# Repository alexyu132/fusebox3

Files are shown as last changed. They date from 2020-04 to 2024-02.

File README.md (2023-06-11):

:warning: **Still under active development**: Parts and documentation may change!
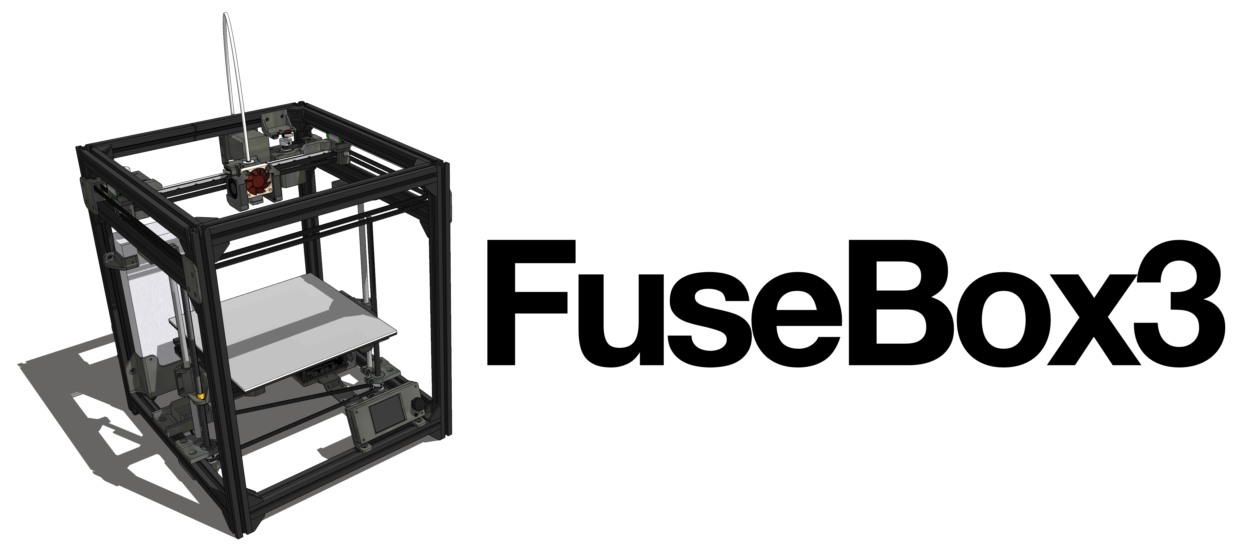
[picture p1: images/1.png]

## The latest in the FuseBox line of 3D printers.

FuseBox3 is a midsize CoreXY printer designed for fast printing and high output quality.

Specs:
- Safe build area (XYZ): 235x235x235mm (Absolute max travels: 238x238.75x238mm)
- Frame dimensions (XYZ): 350x372x427mm
- CoreXY movement system running on MGN9/MGN12 rail
- 2020 extrusion frame
- E3D v6 type hotend with Bowden extruder
- Dual leadscrew, belt-driven z-axis
- Dual 4010 blower print cooling + 4010 axial fan hotend cooling

## Quick Links
### [BOM](documentation/BOM.md)

# Design and changes from FuseBox2/R
While the original FuseBox and FuseBox2 were optimized for simplicity and low build cost, FuseBox3 targets a more premium price point without being overly expensive. However, accessibility and ease of construction is still a priority. Therefore, the printer needs no custom CNC'd parts, and all parts were picked to be easily sourceable online.

### Linear rails
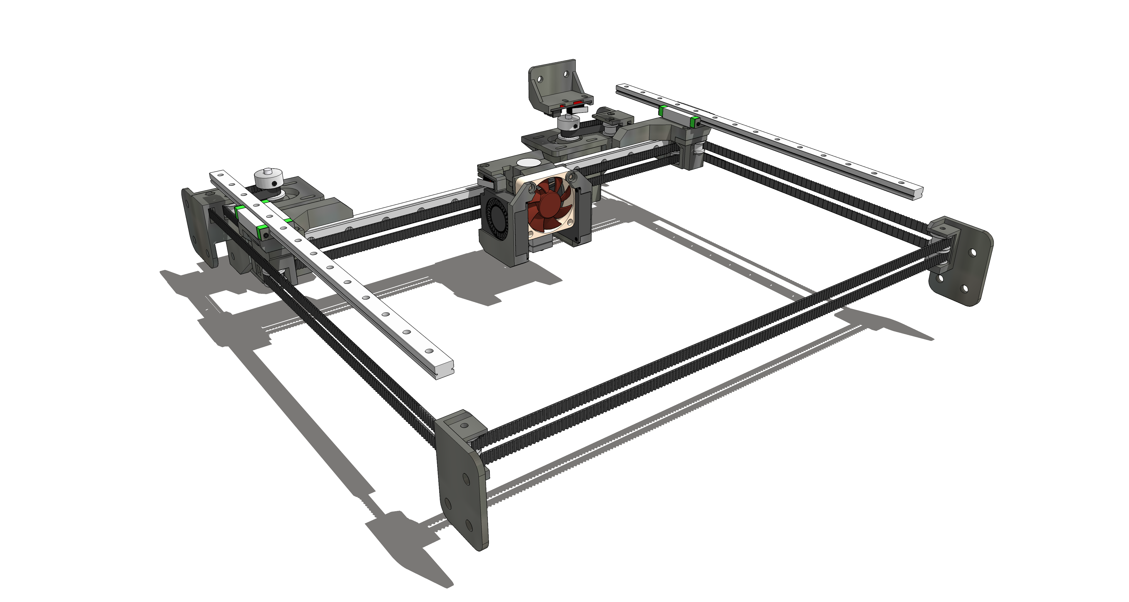
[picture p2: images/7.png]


With MGN-style linear rails becoming cheaper and more easily available, the CoreXY movement has been redesigned to ride completely on rails - the y-axis now uses MGN9 rails screwed directly to the extrusions, which improves rigidity compared to the old linear rods. Like on the Fusebox2R, the gantry/x-axis uses a single MGN12 rail, although it's now 50mm longer to account for the additional build area.

### Belt path changes, tensioning improvements
The original FuseBox and FuseBox2 share a similar belt path - the motors are mounted in the corners of the frame, and the motor pulleys serve as the "ends" of the belt path on the back side. This belt path design minimizes the number of idler pulleys needed, at the cost of quite a bit of wasted space in the x direction, necessitating a wider frame.

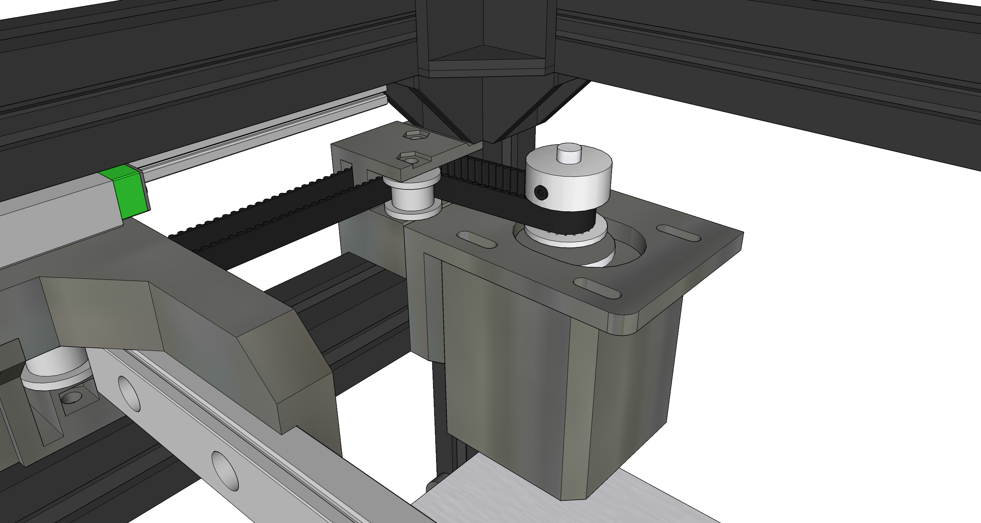
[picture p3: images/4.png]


On the FuseBox3, two additional idlers have been added on the rear (motor) side to bring the belts as close to the sides of the frame as possible. This allows the FuseBox3's frame to be 42mm shorter in the x direction than the FuseBox2R's, while simultaneously having an additional 25mm of x-axis travel. The motors have been relocated to the very back of the machine, just underneath the top rear horizontal extrusion. The motor mounts now have slotted screw holes, allowing them to slide to adjust belt tension. On the FuseBox and FuseBox2, tensioning was done by manually pulling on the belts and sliding them into carriage-mounted belt clamps. The new tensioning system should significantly simplify the belt mounting and tensioning process.

Additionally, the front idler brackets have been changed so that the top and bottom idlers are stacked on top of each other rather than offset. This makes the idlers easier to assemble and saves a bolt and nut on each side.

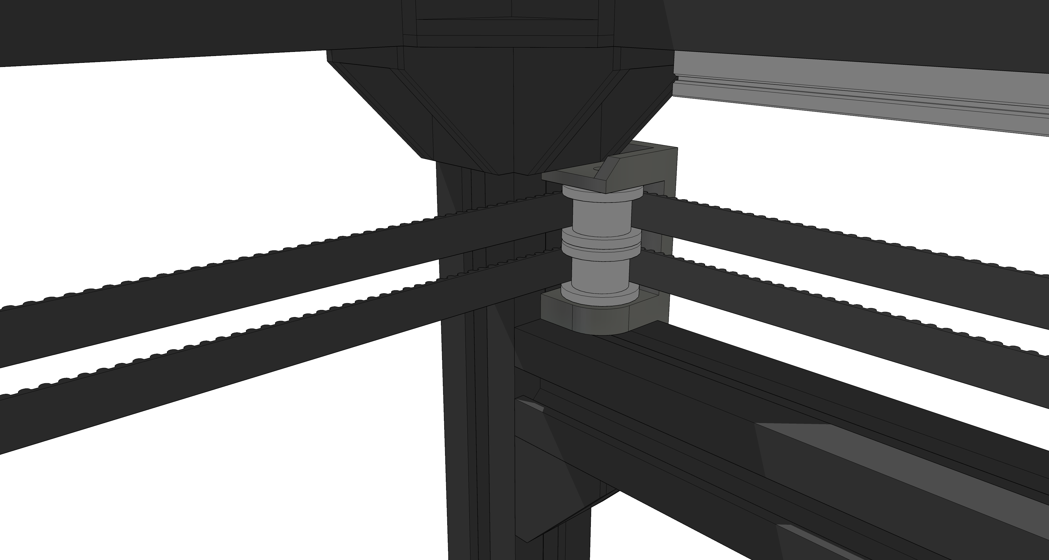
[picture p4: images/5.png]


### Z-axis

The z-axis keeps the 8mm rods due to space and cost constraints, but is now reconfigured as a fully belt-driven setup. On the prototype FuseBox2, the cantilevered z-axis was slightly susceptible to vibration and was also susceptible to banding if lower quality leadscrews or bearings were used. The new design's rods have been relocated to the sides of the printer, with each end driven by its own belt loop. These are connected to a single Z motor, which drives them via a 4:1 reduction pulley. The belted design eliminates banding artifacts and greatly increases the max Z speeds achievable.

### Hotend carriage, print cooling
The general arrangement of FuseBox3's carriage is very similar to the carriage on the older FuseBox2R, with the main differences being the print cooling setup and the belt mounting method. Subjectively, it's also a lot tidier in appearance than the earlier carriage designs.

Like the carriage on the FuseBox2R, the new carriage keeps the mass vertically centered on the rail, with the belts also centered and kept as close to the rail as possible. This design minimizes any twisting of the print head during sharp directional changes.

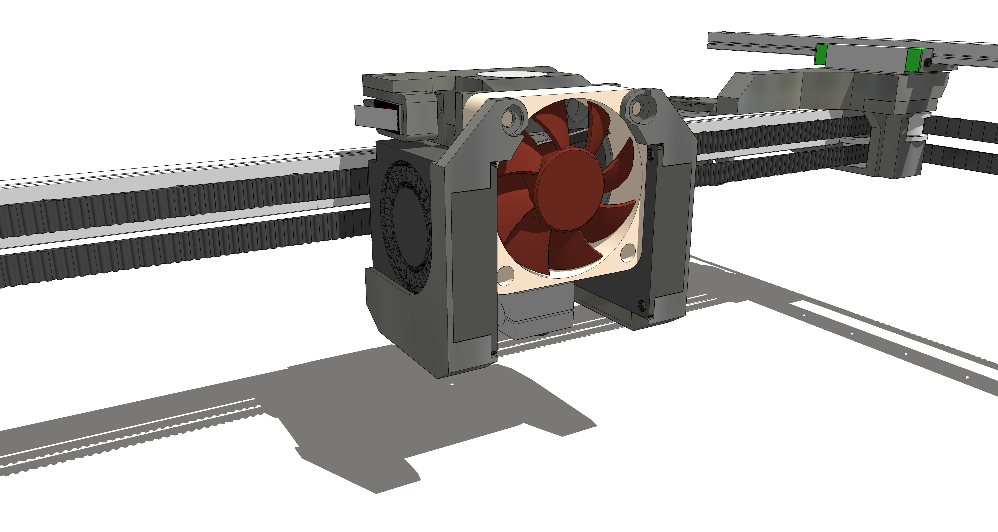
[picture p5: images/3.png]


Since the FuseBox3 has sliding motor mounts, tensioning is no longer done on the carriage. The belts are now attached to the carriage by a pair of clamp pieces that screw into the main carriage body. The clamps have a small cutout on the inner side for routing excess belt, so the belts don't have to be shaved to a precise length like they do on the FuseBox2R.

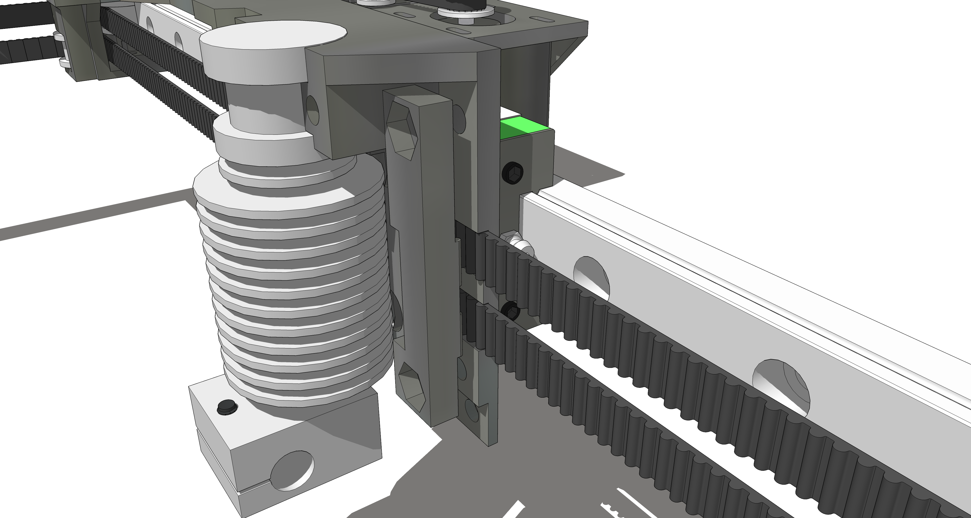
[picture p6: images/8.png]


The print cooling setup swaps out the single 4020 blower for twin 4010 blowers flanking the hotend. The old single blower design provided relatively good cooling performance, but the one-sided airflow led to weaker cooling with certain overhang orientations. Twin blowers enable more even part cooling coverage, and the much shorter ducts provide less airflow restriction. The 40mm axial fan for the hotend has been retained, as it provides lower noise than a 30mm fan for equivalent airflow.

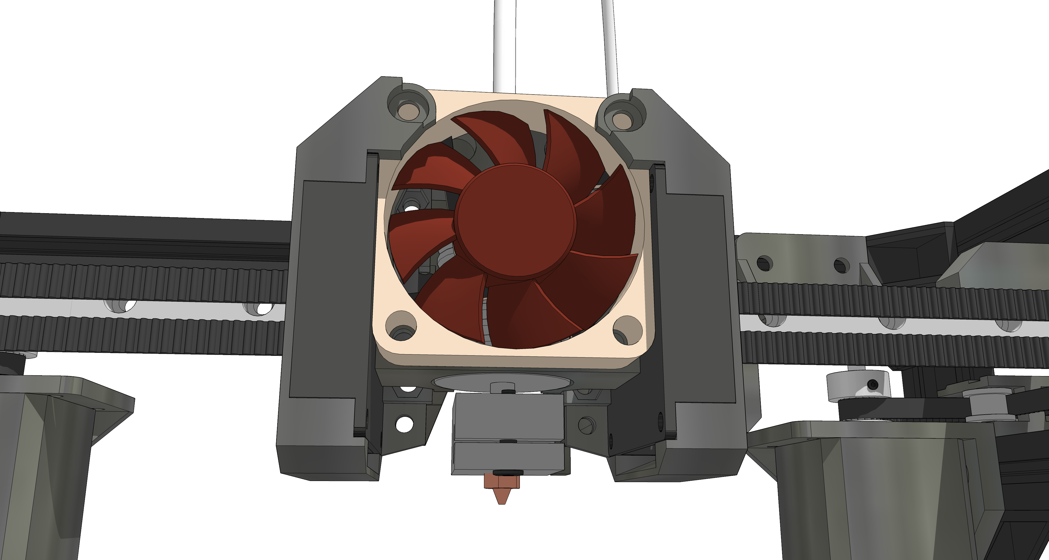
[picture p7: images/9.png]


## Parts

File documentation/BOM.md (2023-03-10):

# Recommended Suppliers (US)
- Extrusions: Misumi (US-based)
- Pulleys, closed loop belts: Powge (Aliexpress)
- Open loop belts: Trianglelab (Aliexpress), Powge (Aliexpress)

# BOM - Non-printed

## Frame
### Extrusions

| Item | Quantity  | Notes|
|---|---|-----|
| 2020 extrusion, 407mm (407mm minimum, these can be increased to 410mm or more to give more room at the bottom of the printer) | 4  | Z axis |
| 2020 extrusion, 332mm | 4  | Y axis. The Y extrusions can be lengthened to increase Y travel without needing to modify any other components. To be able to use 300mm MGN9 rails on the Y axis, the Y extrusions should be at least 345mm, and the top Y extrusions should be at least 385mm. |
| 2020 extrusion, 372mm | 2  | Top Y axis. Must be 40mm longer than Y axis extrusions. |
| 2020 extrusion, 310mm | 4  | X axis |
| 2020 extrusion, 260mm | 2  | Bed X axis |
| 2020 extrusion, 120mm | 2  | Bed Y axis |

### Brackets and fasteners
There are two options for joining frame extrusions. The easiest and quickest, but more expensive, option is to use corner brackets everywhere. The second option is to tap the ends of the extrusions and join them with M5 hardware. This will also require access holes to be drilled through some of the extrusions. Note that this option still requires a few corner brackets to prevent certain extrusions from twisting. The required brackets are marked in yellow in the Sketchup file.

**Option 1: All corner brackets**

| Item | Quantity  |
|---|---|
| Corner bracket (20x20x17mm) | 32 |
| M5x8mm button head | 64 |
| M5 T nut | 64 |

**Option 2: Tapped ends**

| Item | Quantity  |
|---|---|
| Corner bracket (20x20x17mm) | 8 |
| M5x8mm button head | 16 |
| M5 T nut | 16 |
| M5x12mm button head | 24 |
| M5 washer | 24 |

## CoreXY movement (excluding print head)

| Item | Quantity  |
|---|---|
| MGN9 linear rail with MGN9H block, 280mm long (can use 300mm length if Y extrusions are extended, see extrusions section above) | 2 |
| MGN12 linear rail with MGN12C block, 300mm | 1 |
| M3 T nut | 8 |
| M5 T nut | 20 |
| M3x6mm socket head | 8 |
| M3x8mm socket head | 16 |
| M5x8mm button head | 20 |
| M3x10mm button head | 12 |
| M3x20mm button head | 8 |
| M3x30mm button head | 2 |
| M3 nylon lock nut | 22 |
| M3 washer | 8 |
| 16T toothed 2GT idler, 3mm bore | 8 |
| 16T smooth 2GT idler, 3mm bore | 4 |
| 20T 2GT pulley, 5mm bore | 2 |
| 2GT 6mm width belt | 3M |
| NEMA 17 stepper (60+ oz-in/42+ N-cm preferred) | 2 |
| PCB endstop | 1 |

## Print head
| Item | Quantity  |
|---|---|
| M3x6mm socket head | 4 |
| M3x25mm button head | 2 |
| M3x16mm button head | 4 |
| M3x10mm button head | 7 |
| M3 nylon lock nut | 13 |
| E3D V6 or Lite6 hotend (Bowden) | 1 |
| 4010 blower fan (ball bearing recommended) | 2 |
| 4010 axial fan (ball bearing recommended)| 1 |
| Omron D2F-L microswitch (cut one off a PCB endstop) | 1 |

Note: The blower shrouds and axial fan can optionally be attached by zip ties instead of screws. This gets rid of four M3x16mm bolts, two M3x10mm bolts, and six M3 lock nuts.

## Z axis
| Item | Quantity  |
|---|---|
| M3x8mm socket head | 4 |
| M3x10mm button head | 14 |
| M3x20mm button head | 1 |
| M5x8mm button head | 32 |
| M5 T nut | 32 |
| M3 nylon lock nut | 15 | 
| 8mm leadscrew (300mm length, 2mm lead) and brass nut | 2 |
| 300mm length 8mm OD smooth rod | 2 |
| 710mm closed loop 2GT belt, 6mm width | 1 |
| 20T 2GT pulley, 8mm bore | 2 |
| 20T 2GT pulley, 5mm bore | 1 |
| LM8LUU bearing | 2 |
| 608 bearing | 4 |
| NEMA 17 pancake stepper (up to 25mm motor body length) | 1 |
| Ender 3 compatible heated bed (235mmx235mm) and leveling hardware (M4x55 or M4x60mm screws, 8mm OD 40mm length springs) | 1 |
| PCB endstop | 1 |

## Power supply
| Item | Quantity  |
|---|---|
| M5x8mm button head | 5 |
| M5 T nut | 5 |
| M4x6mm socket head | 3 |
| M3x10mm button head | 2 |
| M3 nylon lock nut | 2 |
| Meanwell LRS-350-24 power supply | 1 |
| IEC socket with fuse and switch | 1  |
| IEC power cord | 1  |

## Stock extruder (Bowden)
This is pretty much the extruder from the FuseBox2, modified to hang below an extrusion instead of to the side. Can print flexible filament.

| Item | Quantity  |
|---|---|
| M5x8mm button head | 2 |
| M5 T nut | 2 |
| M3x8mm socket head | 3 |
| M3x10mm button head | 1 |
| M3x25mm button head | 1 |
| M3 nylon lock nut | 1 |
| Stiff spring | 1 |
| 625 bearing | 1 |
| MK8 extruder gear | 1 |
| NEMA 17 stepper (60+ oz-in/42+ N-cm preferred) | 1 |
| PC4-M6 Bowden coupler | 1 |

## Controller and LCD

### BTT SKR and TFT24
| Item | Quantity  |
|---|---|
| M5x8mm button head | 5 |
| M5 T nut | 5 |
| M3x25mm button head | 4 |
| M3x10mm button head | 9 |
| M3 nylon lock nut | 5 |
| M3 nylon standoff, 30mm length | 4 |
| BTT SKR 1.3 or 1.4 | 1 |
| BTT TFT24 LCD | 1 |

## Miscellaneous

| Item | Quantity  |
|---|---|
| 235x235mm print surface (PEI recommended) | 1  |
| Zip ties | Varies  |
| Cable mesh (optional) | Varies  |
| 18AWG wire for AC input | Varies  |
| 14AWG wire for main DC power | Varies  |
| Small binder/bulldog clips for bed | 4  |
| Adhesive felt or rubber feet | 4  |

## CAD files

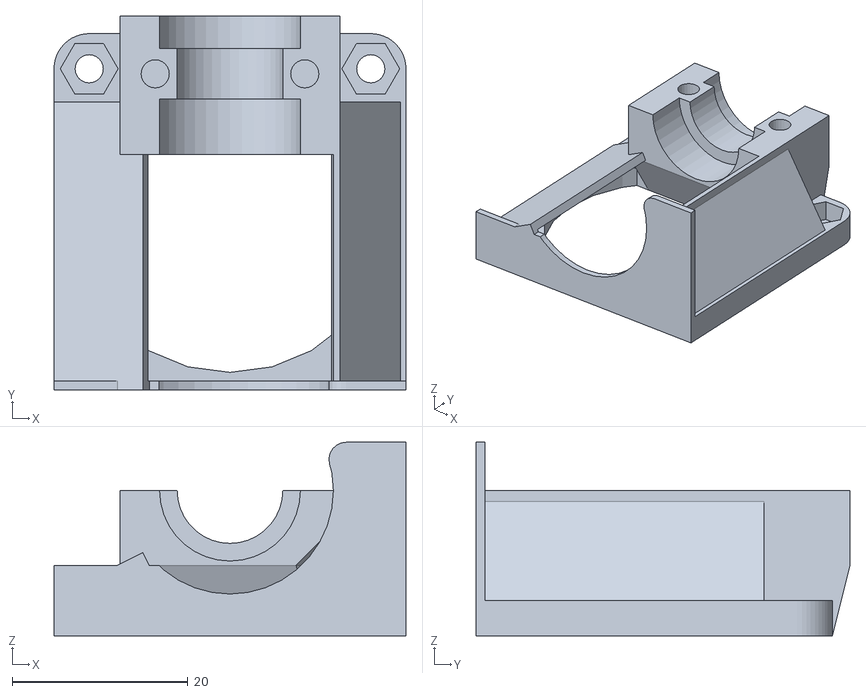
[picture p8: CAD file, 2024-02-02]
stl/carriage/hotend bracket.stl
40.0 x 42.5 x 22.0

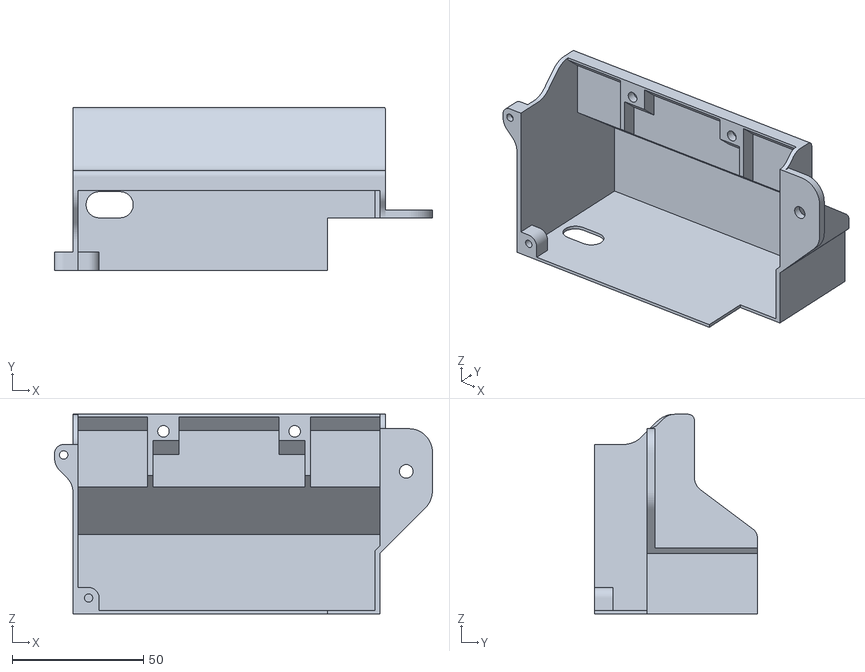
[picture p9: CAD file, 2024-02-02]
stl/electronics/meanwell psu bracket large.stl
144.0 x 62.0 x 76.0

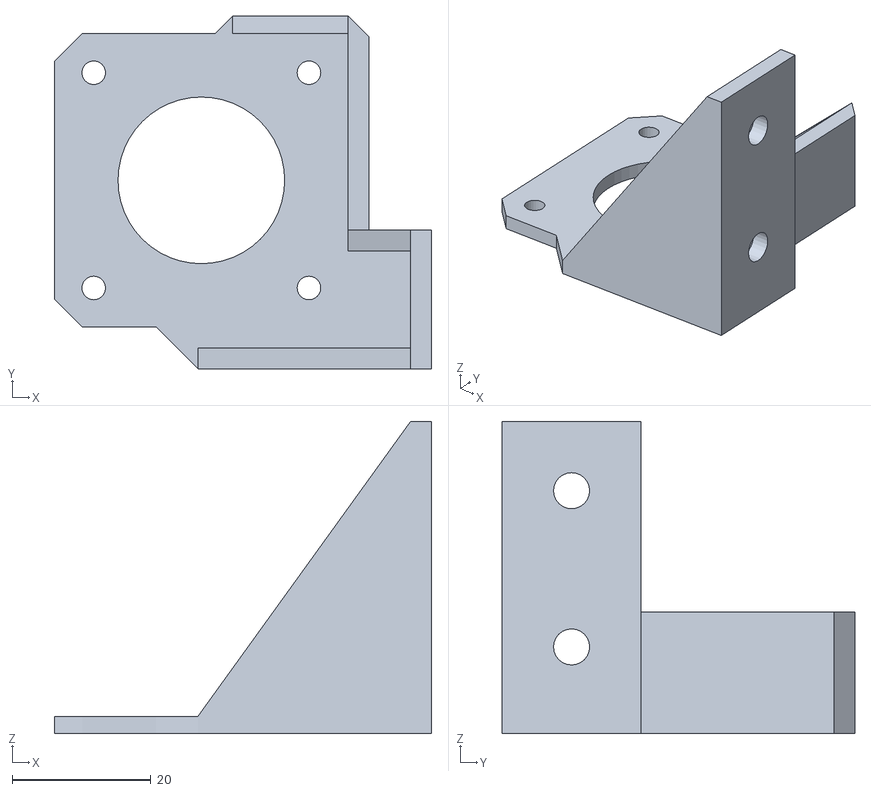
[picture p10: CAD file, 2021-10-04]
stl/extruder/mini bmg mount.stl
54.3 x 50.8 x 45.0

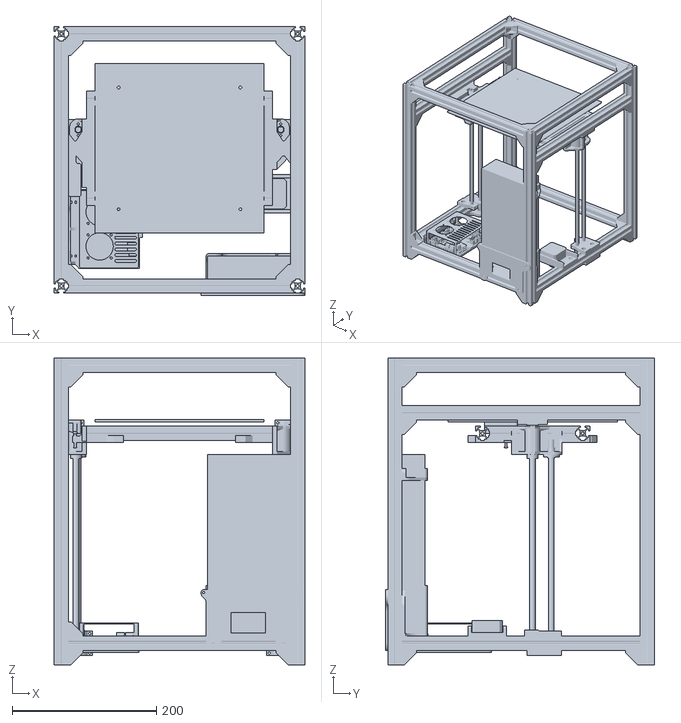
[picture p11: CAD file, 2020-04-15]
stl/fusebox3.stl
348.0 x 373.0 x 426.0

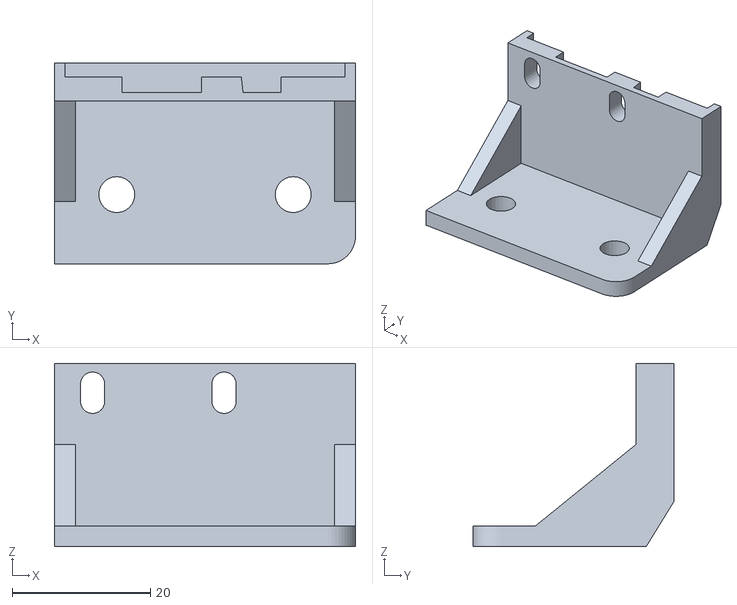
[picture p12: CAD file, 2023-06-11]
stl/gantry/y endstop bracket.stl
43.5 x 29.0 x 26.5

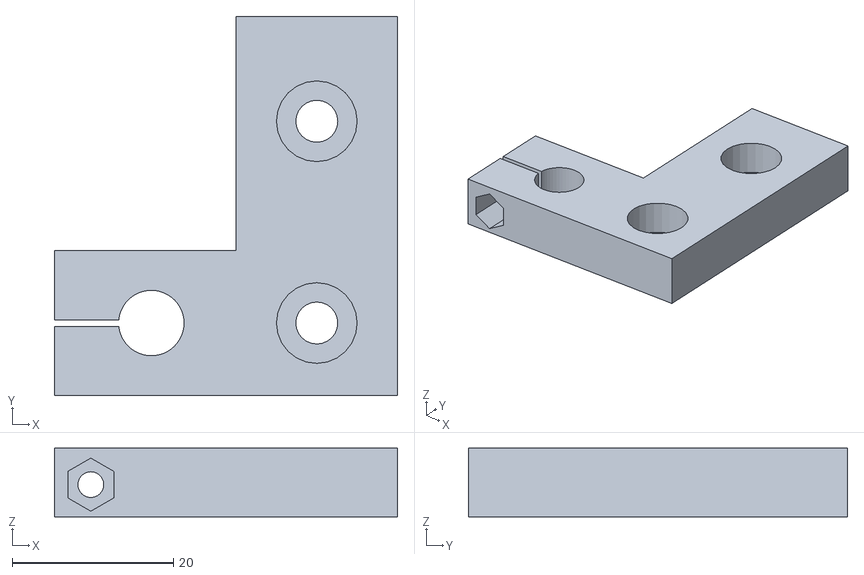
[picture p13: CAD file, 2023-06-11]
stl/z axis/rod mount bottom left.stl
42.5 x 47.0 x 8.50

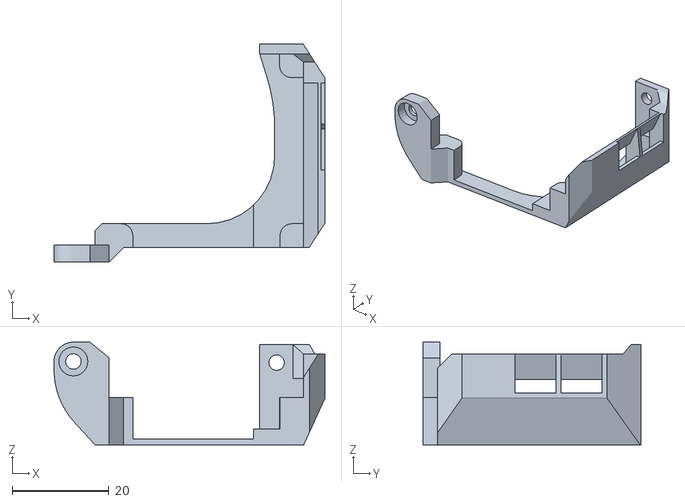
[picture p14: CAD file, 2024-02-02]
stl/carriage/blower mount left.stl
56.0 x 45.0 x 21.3

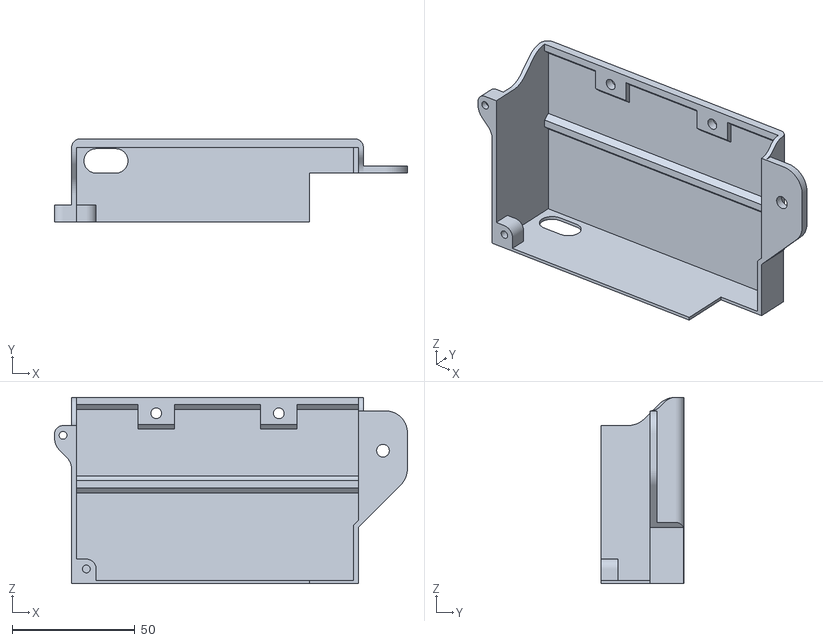
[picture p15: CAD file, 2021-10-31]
stl/electronics/meanwell psu cover.stl
144.0 x 34.0 x 76.0

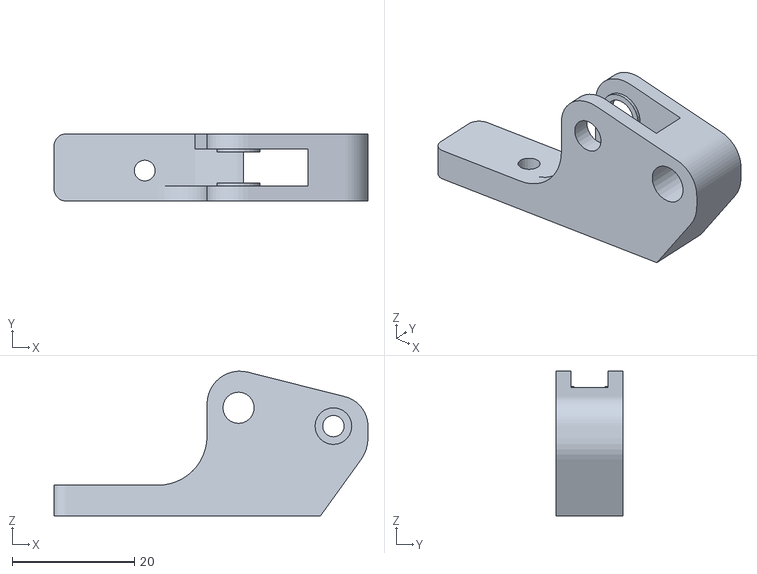
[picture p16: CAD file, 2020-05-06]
stl/extruder/extruder arm.stl
51.3 x 11.0 x 23.6

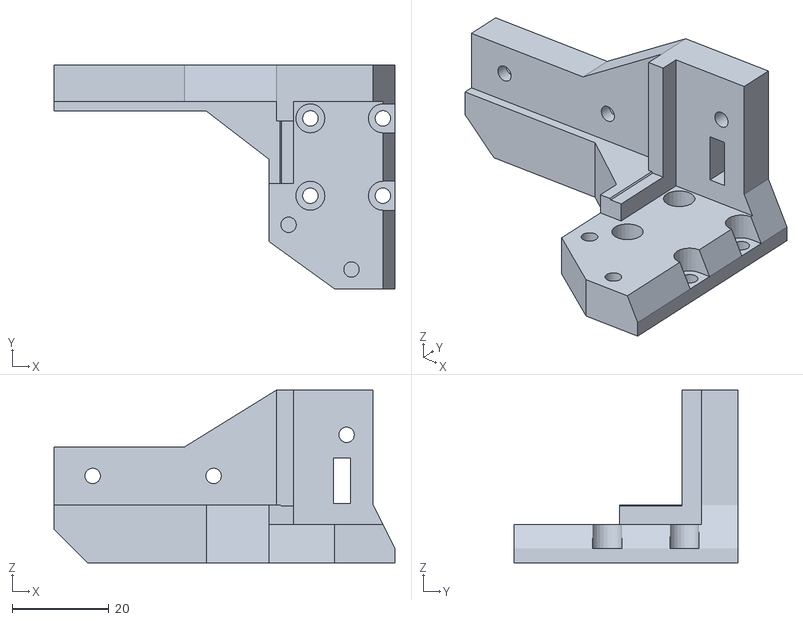
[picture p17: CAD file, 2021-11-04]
stl/gantry/x end left.stl
70.5 x 46.2 x 35.8

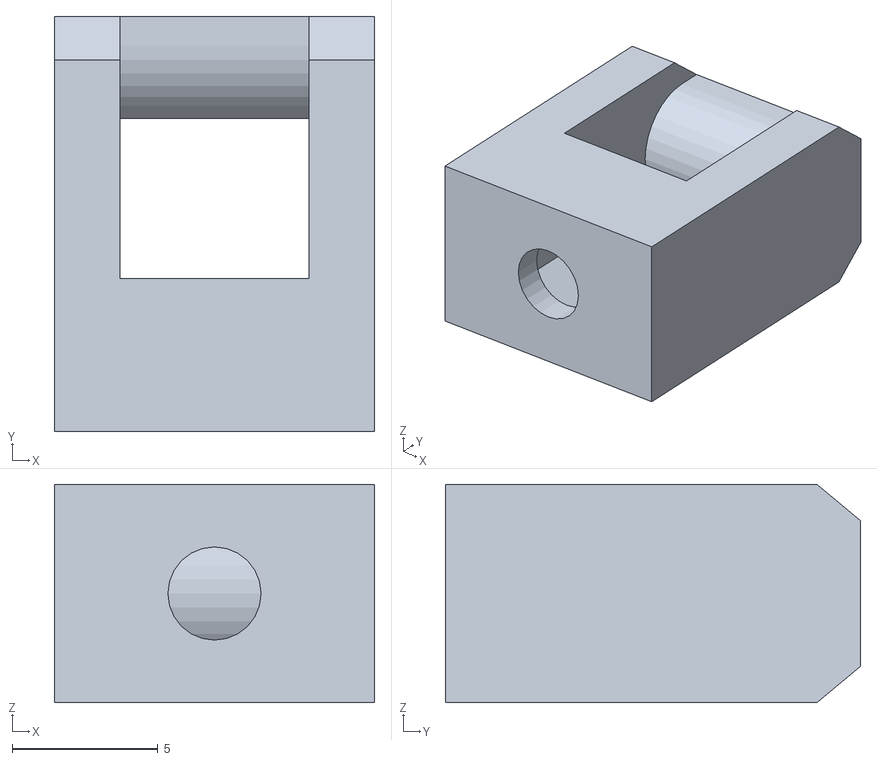
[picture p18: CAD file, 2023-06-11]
stl/z axis/z belt tensioner inner.stl
11.0 x 14.2 x 7.50

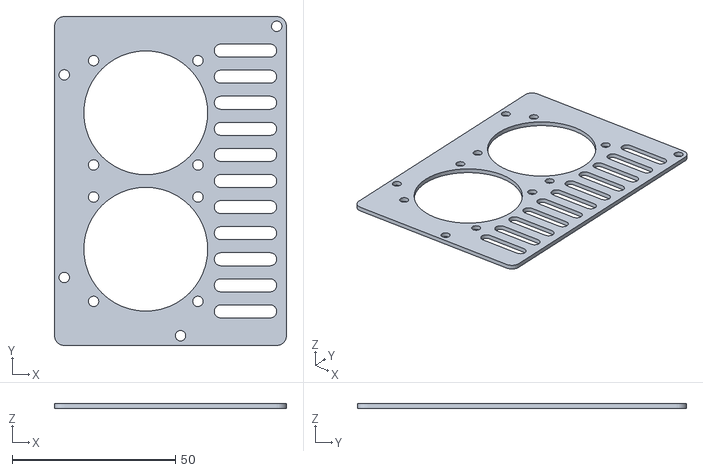
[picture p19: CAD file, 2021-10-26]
stl/electronics/BTT SKR E3 cover.stl
71.2 x 100.9 x 1.50

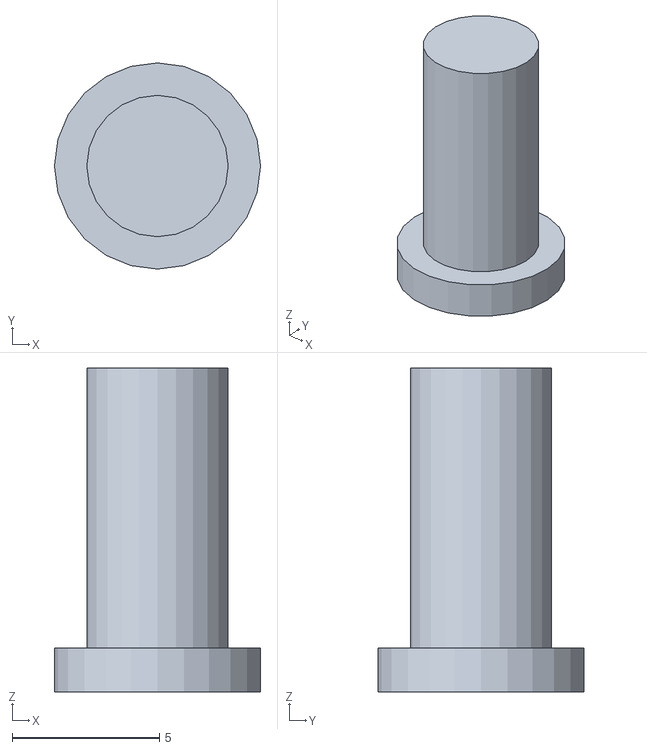
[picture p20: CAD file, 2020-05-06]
stl/extruder/extruder pin.stl
7.00 x 7.00 x 11.0

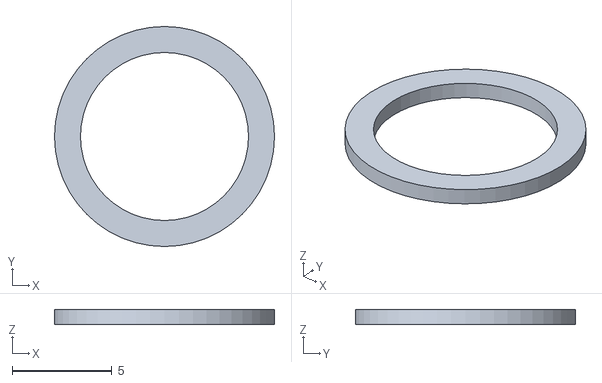
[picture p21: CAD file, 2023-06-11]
stl/z axis/z pulley spacer.stl
11.0 x 11.0 x 0.75

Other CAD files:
stl/carriage/blower mount right.stl
stl/gantry/x end right.stl
stl/carriage/carriage body.stl
stl/electronics/BTT SKR E3 mount.stl
fusebox3.skp
stl/carriage/belt clip left.stl
stl/carriage/belt clip right.stl
stl/carriage/x endstop mount.stl
stl/electronics/BTT SKR cable bar.stl
stl/electronics/BTT SKR cover.stl
stl/electronics/BTT SKR mount.stl
stl/electronics/BTT TFT24 back cover.stl
stl/electronics/BTT TFT24 front cover.stl
stl/electronics/BTT TFT24 mounting bracket left.stl
stl/electronics/BTT TFT24 mounting bracket right.stl
stl/electronics/IEC plate.stl
stl/electronics/PSU cover.stl
stl/electronics/meanwell psu bracket.stl
stl/electronics/top PSU bracket.stl
stl/extruder/extruder body.stl
stl/gantry/front idler left.stl
stl/gantry/front idler right.stl
stl/gantry/front idler spacer.stl
stl/gantry/motor idler left.stl
stl/gantry/motor idler right.stl
stl/gantry/motor mount left.stl
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

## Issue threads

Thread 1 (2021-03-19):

Hello,can you provide the materials to download? Or you can send it to me in the email

qianqiuxx, 2021-03-19:
Hello,can you provide the materials to download? Or you can send it to me in the email

alexyu132, 2021-03-19:
STLs are already provided in the a folder, and the list of materials is in BOM.md in the documentation folder.

Closed 2021-03-19.

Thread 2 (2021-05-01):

Wink and a nudge

Bazmundi, 2021-05-01:
Frame dimensions: ?348x?370xH426mm

Understanding Alex knows but others may not without investigation, can we update info with width and depth?

alexyu132, 2021-05-20:
Hi, sorry for the late response - I was originally planning to build a prototype of this design last year, but ended up postponing that, and am aiming to get one of these built in the next few months. I just pushed a few updates to the design, adjusting some of the extrusion lengths for a bit of extra X/Y travel and increasing belt/idler clearances.

The new dimensions are 350x372x427mm (X,Y,Z).

Closed 2021-05-20.

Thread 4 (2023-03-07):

bed assembly

nsdf7, 2023-03-07:
have this machine built and working great. for the BOM i'd suggest M4x55 or 60 screws and longer springs. this is the only issue i ran into.

alexyu132, 2023-03-10:
Thanks for the info, got a link to those springs? And how close is your bed to the z platform extrusions? On mine I've lowered the gap as much as possible to make sure it has the max possible build area

nsdf7, 2023-03-10:
Here's the springs I used.

MroMax 3D Printer Die Spring 8mm...
https://www.amazon.com/dp/B07YYXN387?ref=ppx_pop_mob_ap_share

Bed to extrusion is about 10mm, I wanted to leave some room allow for
heated insulation.

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

alexyu132, 2023-03-10:
Thanks, updated the BOM with recommendation

Closed 2023-03-10.

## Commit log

2020-02-20 Initial skp file
    [fusebox3.skp]
2020-03-19 test corexy
    [fusebox3.skp]
2020-03-19 update corexy
    [fusebox3.skp]
2020-03-22 new frame
    [fusebox3.skp]
2020-03-22 motor pulley test
    [fusebox3.skp]
2020-03-24 gantry pulley refinement
    [fusebox3.skp]
2020-03-24 idlers, gantry
    [fusebox3.skp]
2020-03-24 adjust extrusion lengths
    [fusebox3.skp]
2020-03-24 motor mount
    [fusebox3.skp]
2020-03-25 motor mounts and motor idlers
    [fusebox3.skp]
2020-03-26 Motor idler refinement, color coding
    [fusebox3.skp]
2020-03-26 Begin carriage
    [fusebox3.skp]
2020-03-26 carriage work
    [fusebox3.skp]
2020-03-26 belt clamps, carriage
    [fusebox3.skp]
2020-03-27 carriage, begin endstops
    [fusebox3.skp]
2020-03-27 x endstop
    [fusebox3.skp]
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2020-03-28 Label bolt lengths, minor fan mount tweaks
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2020-03-29 modify leadscrew spacing, add reinforcement brackets to X
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2020-03-29 adjust y rail length, color
2020-03-29 Fix motor idler dimension
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2020-04-04 adjust z belt length
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2020-04-05 loosen bed screw clearance, switch extrusion colors
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2020-04-15 adjust pulley clearances on x ends
2020-04-15 fix hotend cooling duct
2020-04-15 arrange corexy parts for printing
2020-04-15 Add stls
    [IEC plate.stl, PSU cover.stl, SKR cover.stl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]
2020-04-15 Add LCD case and cable bar
    [BTT SKR cable bar.stl, BTT SKR cover.stl, BTT SKR mount.stl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]
2020-04-17 Adjust x end thicknesses
    [x end left.stl, x end right.stl]
2020-04-17 Add models for lcd and iec plug/switch
2020-04-28 Thicken x ends by 1mm
    [x end left.stl, x end right.stl]
2020-05-03 Round corners on hotend shroud
    [hotend cooling shroud.stl]
2020-05-03 Add zip tie cutouts for cooling shroud
    [hotend cooling shroud.stl]
2020-05-03 Tweak cooling shroud
    [hotend cooling shroud.stl]
2020-05-03 Add additional bolt connection to PSU shroud assembly
    [IEC plate.stl, PSU cover.stl]
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2020-05-06 Add stock extruder
    [extruder arm.stl, extruder body.stl, extruder pin.stl]
2020-08-16 minor strengthening of certain parts
    [front idler left.stl, front idler right.stl, motor idler left.stl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]
2021-03-06 Remove 4 corner brackets on bottom
2021-03-06 Slightly thicken bed mounts
    [bed mount 1.stl, bed mount 2.stl]
2021-05-19 Increase belt spacing and clearances, adjust bed mount extrusion lengths, misc minor adjustments
    [belt clip left.stl, belt clip right.stl, blower mount left.stl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]
2021-05-19 Increase frame X and Y size by 2mm for 2mm extra X/Y travel (238x238.75 max), increase bed side extrusion length from 159 to 160mm
    [BTT SKR cable bar.stl, bed mount 1.stl, bed mount 2.stl]
2021-05-19 Add front idler spacer, update readme
    [front idler spacer.stl]
2021-05-20 Add additional clearance to x ends
    [x end left.stl, x end right.stl]
2021-05-21 Adjust screw lengths for easier sourcing of parts
    [motor idler left.stl, motor idler right.stl, x pulley mount left.stl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]
2021-05-22 Additional clearance for z leadscrew nut
    [z end left.stl, z end right.stl]
2021-06-21 Idler mount adjustments
    [front idler left.stl, front idler right.stl, front idler spacer.stl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]
2021-06-21 Additional x pulley mount clearance to account for bridging droop
    [x pulley mount left.stl, x pulley mount right.stl]
2021-06-26 tweak blower mount for better printing
    [blower mount left.stl, blower mount right.stl]
2021-06-26 hotend cooling shroud printability improvements
    [hotend cooling shroud.stl]
2021-06-27 x end printability improvements, add 3 point leveling option
    [3 point front bed mount.stl, x end left.stl, x end right.stl]
2021-09-16 z axis fixes, fix screw dimension labels in model
    [3 point front bed mount.stl, bed mount 1.stl, bed mount 2.stl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]
2021-09-21 Z axis improvements
    [rod mount bottom left.stl, rod mount bottom right.stl, z end left.stl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]
2021-09-26 fix blower mounts
    [blower mount left.stl, blower mount right.stl]
2021-10-04 carriage body strengthening, z endstop adjuster clearance adjustment
    [carriage body.stl, z endstop adjuster bracket.stl]
2021-10-04 add mount for mini BMG
    [mini bmg mount.stl]
2021-10-04 fix bmg mount stl
    [mini bmg mount.stl]
2021-10-07 Fix z pulley spacer stl
    [z pulley spacer.stl]
2021-10-08 Tighter clearances on z endstop adjuster
    [z endstop adjuster bracket.stl]
2021-10-10 improve blower ducts
    [blower mount left.stl, blower mount right.stl]
2021-10-10 minor gantry/carriage strengthening
    [hotend retaining bracket.stl, motor idler left.stl, motor idler right.stl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]
2021-10-10 add alignment tab to right motor idler bracket, minor idler bracket strengthening
    [front idler left.stl, front idler right.stl, motor idler left.stl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]
2021-10-10 z end tweaks
    [z end left.stl, z end right.stl]
2021-10-14 add meanwell psu mounting parts
    [meanwell psu bracket.stl, meanwell psu cover.stl]
2021-10-15 save some filament on meanwell psu cover
    [meanwell psu cover.stl]
2021-10-24 update meanwell cover to allow extra corner bracket
    [meanwell psu cover.stl]
2021-10-24 save some filament on iec plate
    [IEC plate.stl]
2021-10-25 motor idler tweak
    [motor idler left.stl]
2021-10-26 Add mounting hardware for SKR E3
    [BTT SKR E3 cover.stl, BTT SKR E3 mount.stl]
2021-10-28 Gantry bracket strength improvements, minor z end tweaks
    [front idler left.stl, front idler right.stl, motor idler left.stl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]
2021-10-31 increase psu cover opening size
    [meanwell psu cover.stl]
2021-10-31 Update extrusion lengths to simplify assembly
2021-11-04 tweak x ends
    [x end left.stl, x end right.stl, x pulley mount left.stl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]
2021-11-07 combine hotend retaining bracket and cooling fan shroud into single piece
    [hotend bracket.stl, hotend cooling shroud.stl, hotend retaining bracket.stl]
2022-03-17 Improve Z axis
    Live hinge design to eliminate linear bearing binding; greater clearances for Z nut, leadscrews moved 3mm closer to z rods
    [lower bearing holder left.stl, lower bearing holder right.stl, rod mount bottom left.stl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]
2022-04-05 Loosen top z bearing mount to mitigate z wobble
    [rod mount bottom left.stl, rod mount bottom right.stl]
2022-04-05 Tweak blower mount dimensions for easier printing
    [blower mount left.stl, blower mount right.stl]
2022-09-08 Upper and lower pulley parts
2022-09-14 export finished stls
    [lower bearing holder left.stl, lower bearing holder right.stl, rod mount bottom left.stl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]
2022-10-30 strengthen z end belt clamps, add tensioner parts, update stls
    [lower bearing holder left.stl, lower bearing holder right.stl, rod mount bottom left.stl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]
2023-01-16 Increase endstop mount clearances
    [rod mount top right.stl, y endstop bracket.stl]
2023-04-09 strengthen blower mounts
    [blower mount left.stl, blower mount right.stl]
2023-04-12 tweak blower mount to improve bed adhesion
    [blower mount left.stl, blower mount right.stl]
2023-06-11 loosen endstop mount clearances
    [rod mount top right.stl, y endstop bracket.stl]
2023-06-11 strengthen belt clips
    [belt clip left.stl, belt clip right.stl, carriage body.stl]
2024-01-13 improve blower ducts, improve carriage belt clip
    - Blower ducts aimed downward, top guard added to prevent cooling on the heater block
    - Carriage belt clip tooth profile improved to reduce slippage chance
    [belt clip left.stl, belt clip right.stl, blower mount left.stl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]
2024-01-18 re-orient belt clip STLs, add hotend heatsink airflow cutout
    [belt clip left.stl, belt clip right.stl, carriage body.stl]
2024-01-18 space out fan from hotend; add airflow guide
    [blower mount left.stl, blower mount right.stl, hotend bracket.stl]
2024-01-18 aim fan ducts at nozzle more; add additional airflow cutout for hotend cooling
    [blower mount left.stl, blower mount right.stl, carriage body.stl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]
2024-02-02 add large psu cover for spade terminals, improve ducting
    [blower mount left.stl, blower mount right.stl, hotend bracket.stl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]
